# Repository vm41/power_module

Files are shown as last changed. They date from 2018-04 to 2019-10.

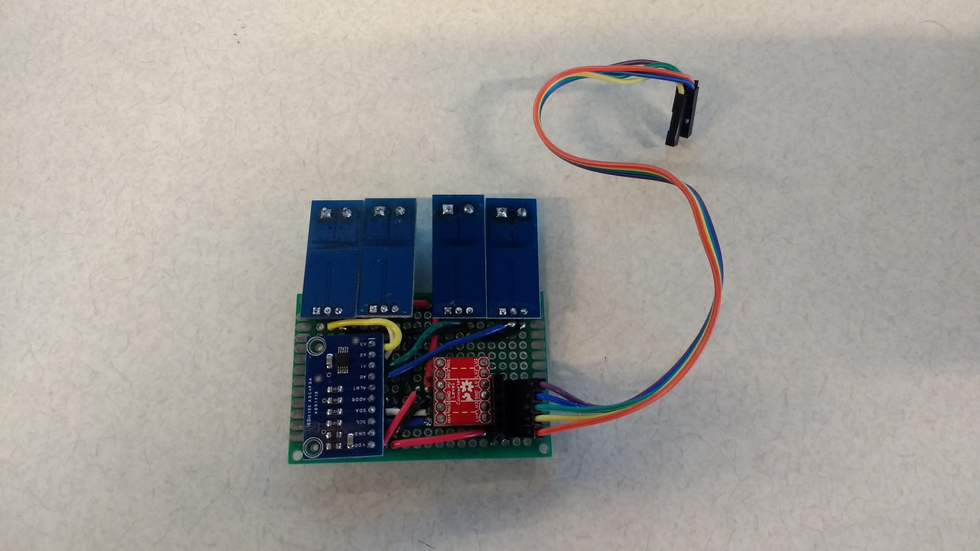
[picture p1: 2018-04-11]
hardware/photos/measurement-module-2.jpg

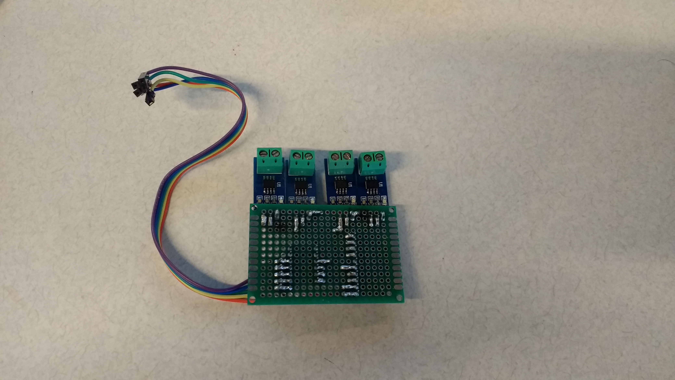
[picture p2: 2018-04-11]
hardware/photos/measurement-module-1.jpg

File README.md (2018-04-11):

# power_module
This repository is intended for use with current_sensing power module.

Documentations for selecting the hardware and instruments can be found in "doc"
Basic test scripts can be found in "i2c-test"

For running measurements:
- measure.py is the code to run on the drone, to measure motors currents, as well as receiving information from the agent, and recording them in log files.
- constant.py is a configuration file imported in measure.py
- tcp_client.py is a test code to run and act as the agent to send some commands to the measure.py manually.

All graph related scripts are in "graph", the ones in 2016 are not necessarily kept anymore, be careful.

---------------------------------------------------
measurement procedure:
* Note that the time of the system is correct before logging. if not, set it manually.
sudo date -s "2017-05-25 00:00"

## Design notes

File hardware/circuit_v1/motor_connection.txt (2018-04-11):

sensors
0	1	2	3
motors connected
B	A	D	C

Blue	Green	Red	Cyan

	^
Red  D	    A   Green

Cyan C      B   Blue

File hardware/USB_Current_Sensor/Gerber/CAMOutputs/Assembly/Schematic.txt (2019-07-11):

Partlist exported from /Users/jerinabr/Google Drive/Eagle_Projects/USB_Current_Sensor/Schematic.sch at 7/11/19 1:01 AM

Qty Value        Device       Package          Parts    Description                                                                            MPN          OC_FARNELL OC_NEWARK PACKAGE  SPICEPREFIX SUPPLIER         
2                2,54/1,0     2,54/1,0         GND, OUT THROUGH-HOLE PAD                                                                                                                                               
1   0.1uF        C-USC1808    C1808            C1       CAPACITOR, American symbol                                                                                                        C                            
1   0.5          R-US_R1206   R1206            R1       RESISTOR, American symbol                                                                                                         R                            
1   2k           R-US_R1206   R1206            R2       RESISTOR, American symbol                                                                                                         R                            
1   629004113921 629004113921 629004113921     K1       WR-COM Plug SMT With Clip USB Type A,4 pins=>Code : Con_I-O_COM_USB-2.0_A_629004113921                                                                         
1   62900416021  62900416021  62900416021      K2       WR-COM SMT Horizontal USB Type A,4 pins=>Code : Con_I-O_COM_USB-2.0_A_62900416021                                                                              
1   INA139NA/250 INA139NA/250 SOT95P280X145-5N U1       High-Side Measurement CURRENT SHUNT MONITOR                                            INA139NA/250 1470398    39C3949   SOT-23-5             Texas Instruments

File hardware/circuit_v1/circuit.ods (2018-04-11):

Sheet: design
 |  |  |  |  |  |  | ---
GND | OUT0 | VCC | GND | OUT1 | VCC |  |  |  | GND | OUT2 | VCC | GND | OUT3 | VCC
 | --- |  |  | --- |  |  |  |  |  | --- |  |  | ---
 |  |  |  |  |  |  |  | ---
 |  |  |  |  |  |  |  |  |  | --- | A3
 |  |  |  |  |  |  |  |  |  | --- | A2
 |  |  | LV1 |  |  | HV1 |  |  |  | --- | A1
 |  |  | LV2 |  |  | HV2 |  |  |  | --- | A0
 |  |  | LV |  |  | HV | --- |  |  |  | #
 |  |  | GND |  |  | GND |  | --- |  |  | ADD
 |  |  | LV3 |  |  | HV3 |  |  |  |  | SDA
 |  |  | LV4 |  |  | HV4 |  |  |  |  | SCL
 |  |  |  |  |  |  |  |  |  |  | GND
 |  |  |  |  |  |  |  |  |  |  | VCC

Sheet: TOP
 |  | --01-- |  |  |  | --01-- | --04-- | --02-- |  |  |  |  | --02-- | --03-- |  |  | --03--
GND | OUT0 | VCC |  | GND | OUT1 | VCC |  |  |  |  | GND | OUT2 | VCC |  | GND | OUT3 | VCC
--11-- | --- |  |  | --12-- | --- |  |  |  |  | --12-- | --13-- | --- |  |  | --13-- | ---
 |  |  |  | --11-- |  |  |  |  |  | --14--
 |  |  |  |  |  |  |  |  |  |  |  | --- | A3
 |  |  |  |  |  |  |  |  |  |  |  | --- | A2
 |  |  | LV1 |  |  |  | HV1 |  |  |  |  | --- | A1
 |  |  | LV2 |  |  |  | HV2 |  |  |  |  | --- | A0
 |  |  | LV |  |  |  | HV | --04-- | --05--
 |  |  | GND |  |  |  | GND | --16-- |  |  | --14-- | --15-- | ADD
 |  |  | LV3 |  |  |  | HV3 | --- |  |  |  | --- | SDA
 |  |  | LV4 |  |  |  | HV4 | --- |  |  |  | --- | SCL
 |  |  | --06-- |  |  |  |  |  |  |  | --16-- | --15-- | GND
 |  |  |  |  |  |  |  |  |  |  | --06-- | --05-- | VCC

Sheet: BACK
--03-- |  |  | --03-- | --02-- |  |  |  |  | --02-- | --04-- | --01-- |  |  |  | --01--
VCC | OUT3 | GND |  | VCC | OUT2 | GND |  |  |  |  | VCC | OUT1 | GND |  | VCC | OUT0 | GND
 | --- | --13-- |  |  | --- | --13-- | --12-- |  |  |  |  | --- | --12-- |  |  | --- | --11--
 |  |  |  |  |  |  | --14-- |  |  |  |  |  | --11--
 |  |  |  | A3 | ---
 |  |  |  | A2 | ---
 |  |  |  | A1 | --- |  |  |  |  | HV1 |  |  |  | LV1
 |  |  |  | A0 | --- |  |  |  |  | HV2 |  |  |  | LV2
 |  |  |  |  |  |  |  | --05-- | --04-- | HV |  |  |  | LV
 |  |  |  | ADD | --15-- | --14-- |  |  | --16-- | GND |  |  |  | GND
 |  |  |  | SDA | --- |  |  |  | --- | HV3 |  |  |  | LV3
 |  |  |  | SCL | --- |  |  |  | --- | HV4 |  |  |  | LV4
 |  |  |  | GND | --15-- | --16-- |  |  |  |  |  |  |  | --06--
 |  |  |  | VCC | --05-- | --06--

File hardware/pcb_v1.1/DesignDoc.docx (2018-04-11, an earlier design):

# overview

The objective of this project is to create a digital system capable of monitoring the power usage of multiple components involved in the operation of an autonomous unmanned aerial vehicle. The device will measure and record the power draw of each component to allow for accurate modeling of the system’s power consumption. In order to ensure accurate measurements without impeding the aircrafts operation the system should be lightweight and draw minimal power.

# design parameters

- Measure current draw of up to 20A
- High precision and accuracy measurements
- Record current draw of 8 separate devices
- Sample data points regularly at high speed
- Pass measurements to a higher level controller via I²C
- Support 3.3V and 5V logic systems
- Minimal weight/size
- Minimal power consumption

# block diagram

The first key components of the system are a set of eight current sensing devices. These sensors will be placed on the high side of each device to be measured and generate an analog output between ground and the logic voltage proportional to the current draw of the attached load. These analog values will then be sampled by an analog to digital converter (ADC) and the resulting digital values will be transmitted via an I²C serial interface to the high level controller.

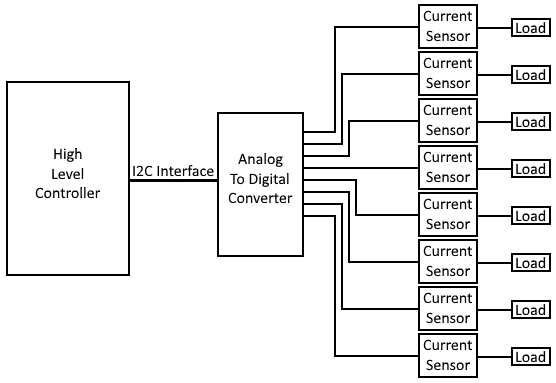
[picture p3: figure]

# Component selection

### A Note on Operating Voltage:

While the system as a whole needs to be able to operate on both 3.3V and 5V logic levels, this restriction is not necessarily needed for the operating voltage of all components in the system. As part of the I²C interface the master device pulls the clock and data lines high to its supply voltage. For some systems this is 3.3V while for others it is 5V. Conveniently this means that the logic voltage of the slave devices is not relevant (so long as it can handle the high voltage of the master) as it will only ever be pulling these lines down to ground, not up to its supply voltage. For example the Raspberry Pi is a 3.3V logic system, however this can be connected via I²C to an Arduino device operating with 5V logic. This is possible as logical high from the Raspberry Pi is 3.3V which falls above the 3V cutoff for the Arduino’s logical high.

As the entirety of this system is isolated from the master device by the I²C bus this allows us to choose components that operate on a standard 5V. This higher supply voltage allows the I²C interface to be operated with both 5V and 3.3V masters, provides greater dynamic range when generating analog voltages, and more greatly increases the list of available components to choose from. If 5V is not available in a given implementation an inline buck/boost converter can be added to regulate the supply voltage to 5V. A device like this devices is already integrated into the Raspberry Pi which provides a 5V output.

## Analog to Digital Converter:

The analog to digital converter used in this system will need to be able to receive 8 analog inputs and convert them to high precision digital values. This readings must be refreshed regularly to ensure that measurements reflect the changing current draw of each load. The device must also support an I²C interface to communicate with the high level controller.

### Resolution:

The accuracy of an ADC is largely determined by is resolution, the number of bits used to represent the digital values it generates. A higher resolution is desired as it directly increases a devices ability to sample an analog value accurately. For this implementation a resolution of 12 bits or more is likely desirable, this will guarantee accuracy within ~1.22 mV.

accuracy=(vcc)/(2^(resolution))=(5V)/(2^12)≈0.0012207 V

### Sampling Rate:

The sampling rate is the rate at which an ADC can convert analog values to digital ones. While this metric is not highly critical it is a factor to be considered. A higher sampling rate will allow conversion to be completed faster meaning that measurements will more accurately reflect the state of the system and will allow more data points to be collected. These values are measured in samples per second (S/s or sps) and can range from 10 S/s to 200kS/s depending on the device. A minimum of 1kS/s is recommended, for accuracy down to 1ms as loads may change quickly.

### Recommendation:

Based on these criteria I recommend we use the MAX11614EEE+ (https://www.mouser.com/ProductDetail/Maxim-Integrated/MAX11614EEE%2b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) analog to digital converter. It’s capable of reading 8 channels with 12 bit resolution at 94.4ksps and transmitting the results over I²C to a master operating at 3.3V or 5V. It also comes in a 12 channel version which could be implemented in the future if desired with minimal changes to the design.

## Current Sensor

### Functional Principle

The two most popular types of current sensors are Hall Effect current sensors and Current Shunt Monitors. Hall Effect sensors measure the electromagnetic field created by current flowing through a wire and produce an analog output proportional to the field strength. Shunt monitors pass the current over a small resistor and generate an analog output proportional to the voltage drop across the resistor, this allows the current flow to be calculated easily by Ohm’s law. These systems over differing tradeoffs between accuracy

### Accuracy and Range

The current sensors used in this system must be able to accurately measure currents ranging from 0-20A. Currents ≤ 1A are expected for computational components such as the higher level controller while peak currents of up to 20A may be drawn by the aircrafts motors. Due to this large range it may be difficult to accurately measure low current values.

One possible solution is for the device to have an adjustable gain, this would allow us to adjust the output ratio for each sensor individually and make full use of the sensors output range. For example let us consider a current sensor capable of measuring 0-20A and producing a corresponding output voltage of 0-5V. When connected to a motor drawing the full 20A maximum the sensor would produce an output voltage of 5V. However, when connected to a microcontroller drawing 1A or less the sensor would produce an output of 0.25V. In the second case the sensor is using at most 5% of its output range and in doing so loses accuracy to sample error and voltage fluctuations. Ideally we would adjust the gain of the sensor such that the maximum expected current, in this case 1A, generates the maximum possible output of 5V restoring the devices dynamic range.

While these voltage ranges and adjustable gain are possible with both Hall Effect sensors and shunt monitors, it is far easier to detect a wide range of voltages with a shunt monitor. When using a Hall Effect sensor to accurately measure current flows of <10A it is often necessary to add multi-layer or multi-wind paths as seen in the figure below to concentrate the magnetic field. Without these additions low current readings are likely to be unreliable. Unfortunately these traces are often incapable of handling currents >10A, meaning that we must choose at the time of the board design if a given channel will be able to measure 0A-10A accurately or 10A-20A accurately. This can be problematic if a load varies across these ranges, e.g. if a motor commonly draws 5A-15A.

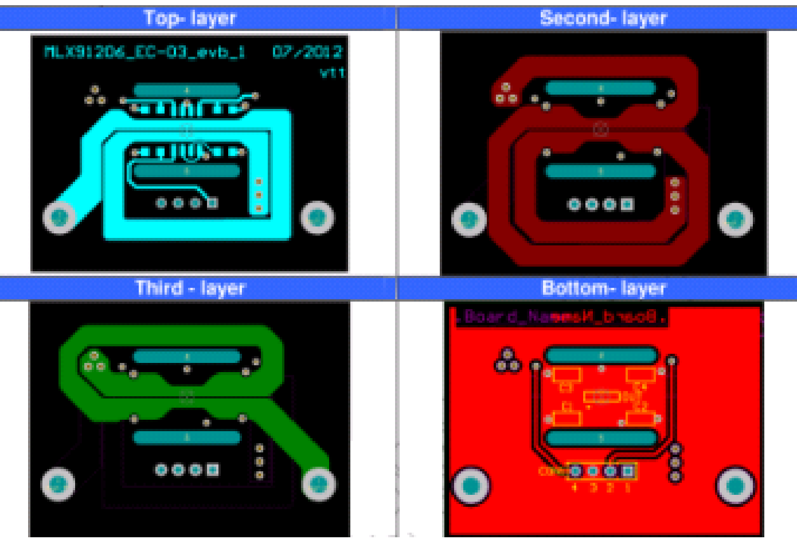
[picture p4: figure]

While Hall Effect sensors are moderately more accurate than shunt monitors given these modifications and proper tuning, shunt monitors are desirable for their ability smoothly measure current flow anywhere within the range set by their gain. The gain can be adjusted at any time simply by replacing a resistor on the output line allowing for precise measurements over a flexible range without requiring a redesign of the board itself.

### Isolation

When considering electrical isolation Hall Effect sensors are clearly superior. As Hall Effect sensors measure the magnetic field generate by the current and not the current directly they are non-intrusive and do not need to actually connect to a components power supply. This provides the benefit of an independent load and measurement system, a failure of one is unlikely to cause damage to the other as they are not physically connected. Contrastingly shunt monitors measure the current flow by passing it across a resistors and therefore need to be placed in line between the load and the voltage supply. Accordingly if a shunt resistor fails it may impede the operation of the load it is attached to, and excessively high load currents may damage the sensor itself. Under normal operation this shouldn’t matter but added isolation of a Hall Effect sensor is beneficial for fault protection.

### Complexity

While both Hall Effect Sensors and shunt monitors require passive components for proper operation, shunt monitors are a simpler a more robust option. A shunt monitor can be quickly and easily implemented with only the IC and two resistors. Hall Effect sensors are significantly more complex to setup accurately with recommended implementations using three capacitors, one resistor and a ferromagnetic shield. The shielding requirement is perhaps the most obtrusive, for accurate readings the manufacturer suggests using a U-shaped metal channel to focus the magnetic field from the load line and prevent interference from other electromagnetic sources. Given the application we can expect these sensors to be in close proximity to other components that will generate interference and make this shielding necessary. Lastly once constructed Hall Effect sensors should be tuned to ensure accurate readings. While these steps can ensure that Hall Effect sensors provide very accurate readings, they increase the chance of a manufacturing error or malfunction.

### Power Consumption

To be completed, want to run some calculations through MATLAB

### Recommendation

To be completed, dependent on results of MATLAB simulation

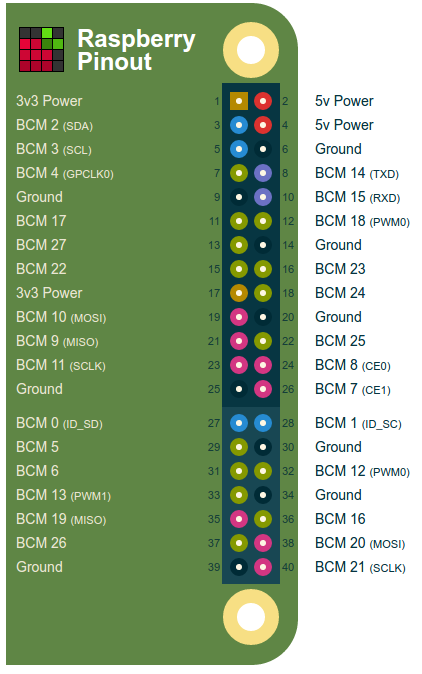
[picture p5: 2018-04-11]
hardware/photos/pi_pinout.png

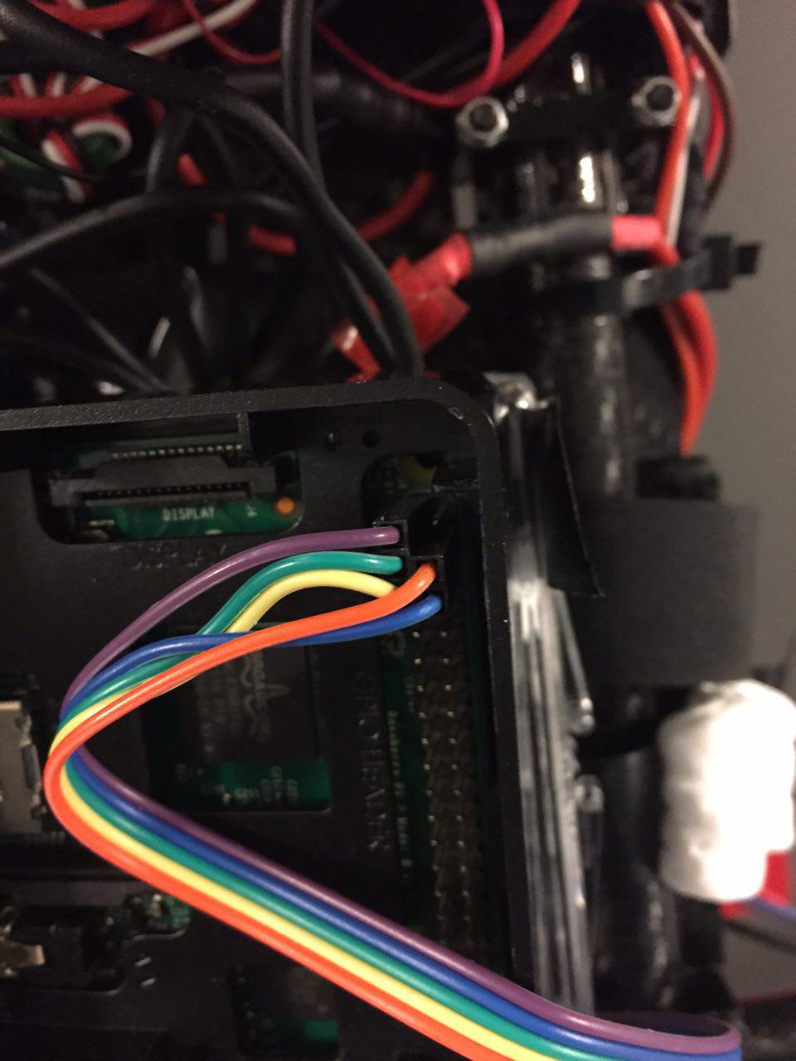
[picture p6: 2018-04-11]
hardware/photos/pi-connection.jpg

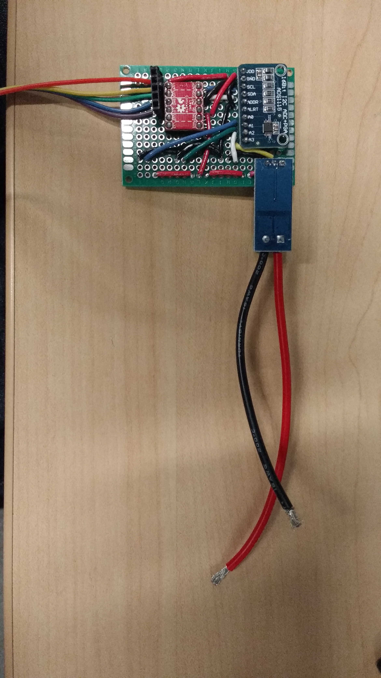
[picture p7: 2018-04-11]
hardware/photos/sensor-polarity-2.jpg

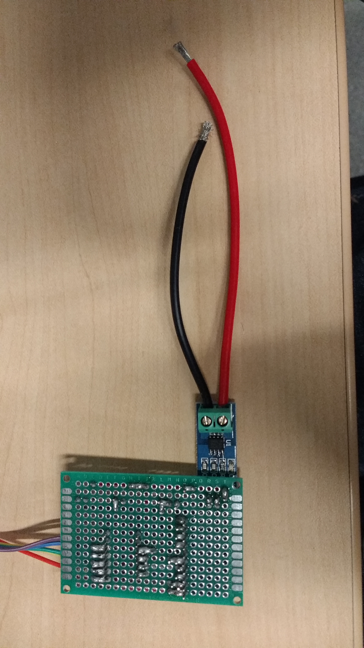
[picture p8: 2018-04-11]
hardware/photos/sensor-polarity-1.jpg

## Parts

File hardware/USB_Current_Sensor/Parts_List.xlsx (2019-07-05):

Number of Boards: | 3
Component | Quantity (per Board) | Quantity (Total) | Part Number | Price (per Part) | Price (Total) | Part Link
Current transducer | 1 | 3 | INA139NA/250 | $2.00 | $6.00 | digikey (https://www.digikey.com/product-detail/en/texas-instruments/INA139NA-250/INA139NA-250CT-ND/379721)
0.5ohm resistor | 1 | 3 | CSR1206FTR500 | $0.42 | $1.26 | digikey (https://www.digikey.com/product-detail/en/stackpole-electronics-inc/CSR1206FTR500/CSR1206FTR500CT-ND/3477074)
2kohm resistor | 1 | 3 | TNPW12062K00BEEA | $0.72 | $2.16 | digikey (https://www.digikey.com/product-detail/en/vishay-dale/TNPW12062K00BEEA/TNP2.00KACCT-ND/1857155)
0.1uF capacitor | 1 | 3 | VJ1808Y104KXCAT | $0.75 | $2.25 | digikey (https://www.digikey.com/product-detail/en/vishay-vitramon/VJ1808Y104KXCAT/720-1129-1-ND/1894475)
USB A Male | 1 | 3 | "629004113921" | $2.21 | $6.63 | digikey (https://www.digikey.com/product-detail/en/wurth-electronics-inc/629004113921/732-3182-5-ND/2627298)
USB A Female | 1 | 3 | "62900416021" | $2.36 | $7.08 | digikey (https://www.digikey.com/products/en?keywords=62900416021)
 |  |  |  | Price (per Board) | Price (Total boards)
 |  |  |  | $8.46 | $25.38

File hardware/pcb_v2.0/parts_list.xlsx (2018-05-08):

Number of Boards | 3 | Multiples of 3 only
Component | Quantity | Extd Quantity | Type/Value | Purpose | Package | Part Number | Price | Extended Price | Link
ADC | 1 | 3 | Analog to Digital Converter | take reads of IN0-IN7 |  | MAX11614EEE+ | $3.580 | $10.74 | mouser (https://www.mouser.com/ProductDetail/Maxim-Integrated/MAX11614EEE%2b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)
Voltage Regulator | 1 | 3 | linear regulator | make 3V3 for I2C bus | SOT-323-5L | LD59015C33R | $0.670 | $2.01 | mouser (https://www.mouser.com/ProductDetail/STMicroelectronics/LD59015C33R)
MOSFET | 2 | 6 | N Ch Enhancement | level shifters for I2C bus | SOT-23-3 | BSS138N H6327 | $0.290 | $0.87 | mouser (https://www.mouser.com/ProductDetail/Infineon-Technologies/BSS138N-H6327)
DC/DC Converter | 1 | 3 | 28V, 1.5A, 1.4MHz Step-Down Converter | buck converter for clean 5V from battery | SOT-23-6 | ACT4088US-T | $0.770 | $2.31 | mouser (https://www.mouser.com/ProductDetail/Active-Semi/ACT4088US-T)
 |  | 0 |  |  |  |  |  | $0.000
Passive Components |  | 0 |  |  |  |  |  | $0.000
Capacitor | 2 | 6 | .1uF ceramic | bypass for ADC vref/vcc | 0603 | VJ0603Y104JXQPW1BC | $0.100 | $0.30 | mouser (https://www.mouser.com/ProductDetail/Vishay-Vitramon/VJ0603Y104JXQPW1BC)
Capacitor | 2 | 6 | 1uF cermic | bypass for 3V3 regulator vcc/output | 0603 | VJ0603G105KXYCW1BC | $0.100 | $0.30 | mouser (https://www.mouser.com/ProductDetail/Vishay-Vitramon/VJ0603G105KXYCW1BC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)
Capacitor | 1 | 3 | undefined, possible .1uF above | voltage divider backup current | 0603 |  | $0.000 | $0.000
Capacitor | 2 | 6 | 22uF | stability of buck converter | 0603 | GRT188R60J226ME13D | $0.510 | 1.530 | mouser (https://www.mouser.com/ProductDetail/Murata-Electronics/GRT188R60J226ME13D?qs=5aG0NVq1C4wtE7eg0bKClQ%3d%3d)
Capactitor | 1 | 3 | 10uF | bypass for buck converter vcc | 0603 | C1608X5R0J106K080AE | $0.320 | 0.960 | mouser (https://www.mouser.com/ProductDetail/TDK/C1608X5R0J106K080AE)
 |  | 0 |  |  |  |  |  | $0.000
Resistor | 2 | 6 | 49.9k | feedback for buck, voltage divider | 0603 | APC0603B49K9N | $0.100 | $0.30 | mouser (https://www.mouser.com/ProductDetail/ARCOL-Ohmite/APC0603B49K9N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)
Resistor | 1 | 3 | 9.65k | feedback for buck, voltage divider | 0603 | RN731JTTD9651B25 | $0.630 | 1.890 | mouser (https://www.mouser.com/ProductDetail/KOA-Speer/RN731JTTD9651B25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)
Resistor | 4 | 12 | 10k | voltage divider pullups | 0603 | AC0603FR-0710KL | $0.016 | $0.05 | mouser (https://www.mouser.com/ProductDetail/Yageo/AC0603FR-0710KL)
 |  | 0 |  |  |  |  |  | $0.000
Inductor | 1 | 3 | 4.7uH | buck converter | 1008 | MLP2520V4R7MT0S1 | $0.420 | 1.260 | mouser (https://www.mouser.com/ProductDetail/TDK/MLP2520V4R7MT0S1)
Schottky Diode | 1 | 3 | 2A If, >28V Vrrm | buck converter | 0603 | NSR20F30NXT5G | $0.500 | 1.500 | mouser (https://www.mouser.com/ProductDetail/ON-Semiconductor/NSR20F30NXT5G)
 |  |  |  |  |  | Total Price Components |  | $24.02

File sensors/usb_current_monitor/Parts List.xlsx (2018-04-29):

No of Boards (mult of 3) | 3
Part | Part No | Quanity | Ext Quantity | Cost | Ext. Cost | Link
Shunt Monitor | INA169NA/3K | 1 | 3 | $2.21 | $6.63 | mouser (https://www.mouser.com/ProductDetail/Texas-Instruments/INA169NA-3K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)
Micro USB Connector | ZX62R-B-5P(30) | 1 | 3 | $0.93 | $2.79 | mouser (https://www.mouser.com/ProductDetail/Hirose-Connector/ZX62R-B-5P30)
USB Type A Connector | UJ2-AH-1-SMT-TR | 1 | 3 | $1.16 | $3.48 | mouser (https://www.mouser.com/ProductDetail/CUI/UJ2-AH-1-SMT-TR)
0.5Ω 0805 Shunt Resistor | LRCS0805-0R5FT5 | 1 | 3 | $0.17 | $0.51 | mouser (https://www.mouser.com/ProductDetail/IRC-TT-Electronics/LRCS0805-0R5FT5)
7.5kΩ 0805 Load Resistor | ERJ-PB6B7501V | 1 | 3 | $0.58 | $1.74 | mouser (https://www.mouser.com/ProductDetail/Panasonic/ERJ-PB6B7501V?qs=sGAEpiMZZMtlubZbdhIBIMNI7sOfyRuJfpLhIIhVJJY%3d)
Optional Headers - Ignore for now |  | 0 | 0 | $0.00 | $0.00
Signal Header Female | 505567-0371 | 0 | 0 | $0.73 | $0.00 | mouser (https://www.mouser.com/ProductDetail/Molex/505567-0371)
Signal Header Male | 505565-0301 | 0 | 0 | $0.25 | $0.00 | mouser (https://www.mouser.com/ProductDetail/Molex/505565-0301)
 |  |  | Total Cost: |  | 15.15

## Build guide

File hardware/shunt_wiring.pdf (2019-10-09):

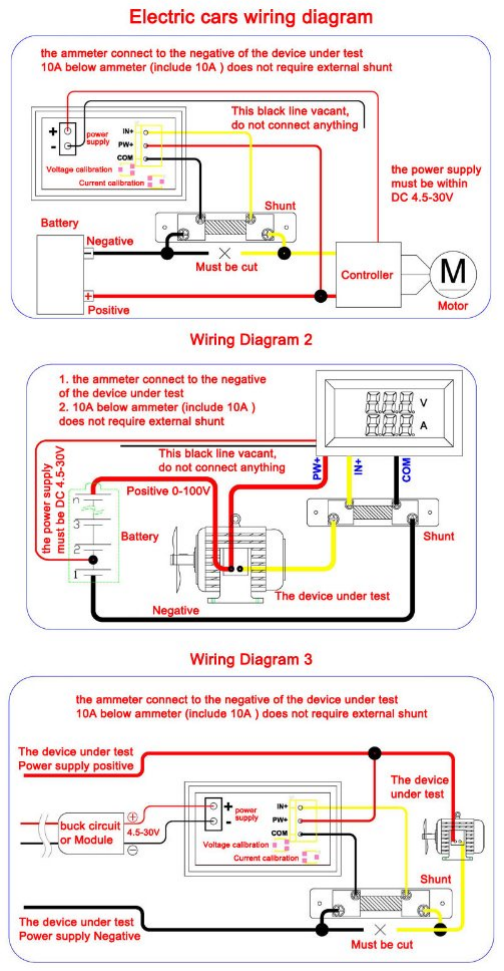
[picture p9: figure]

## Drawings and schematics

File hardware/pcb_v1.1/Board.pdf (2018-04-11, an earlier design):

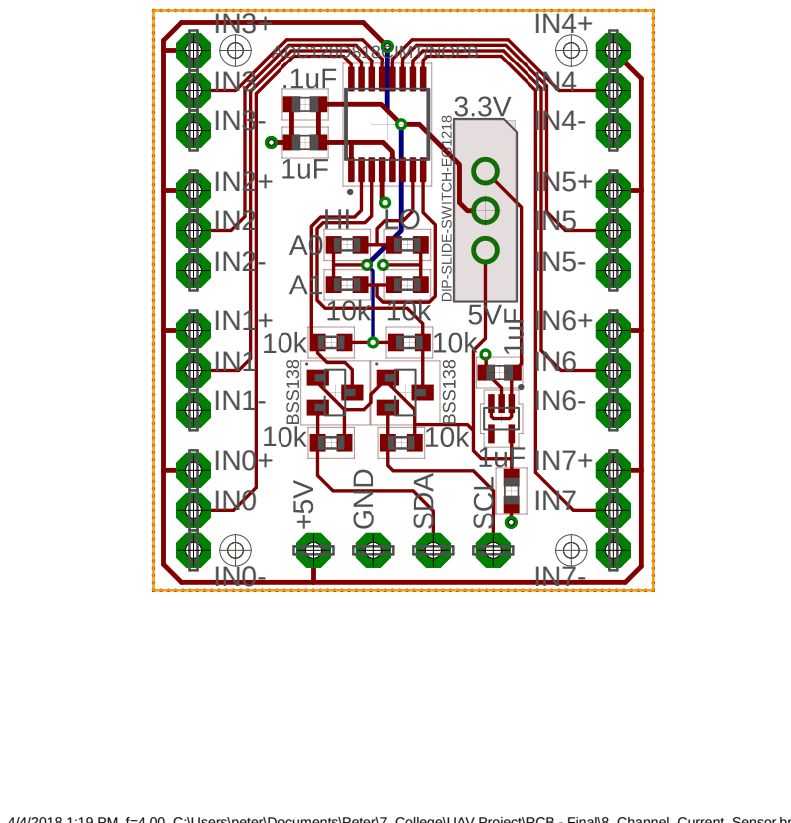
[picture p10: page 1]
GND; SDA; SCL; ADC128D818CIMT/NOPB .1uF

4/4/2018 1:19 PM f=4.00 C:\Users\peter\Documents\Peter\7. College\UAV Project\PCB - Final\8_Channel_Current_Sensor.brd

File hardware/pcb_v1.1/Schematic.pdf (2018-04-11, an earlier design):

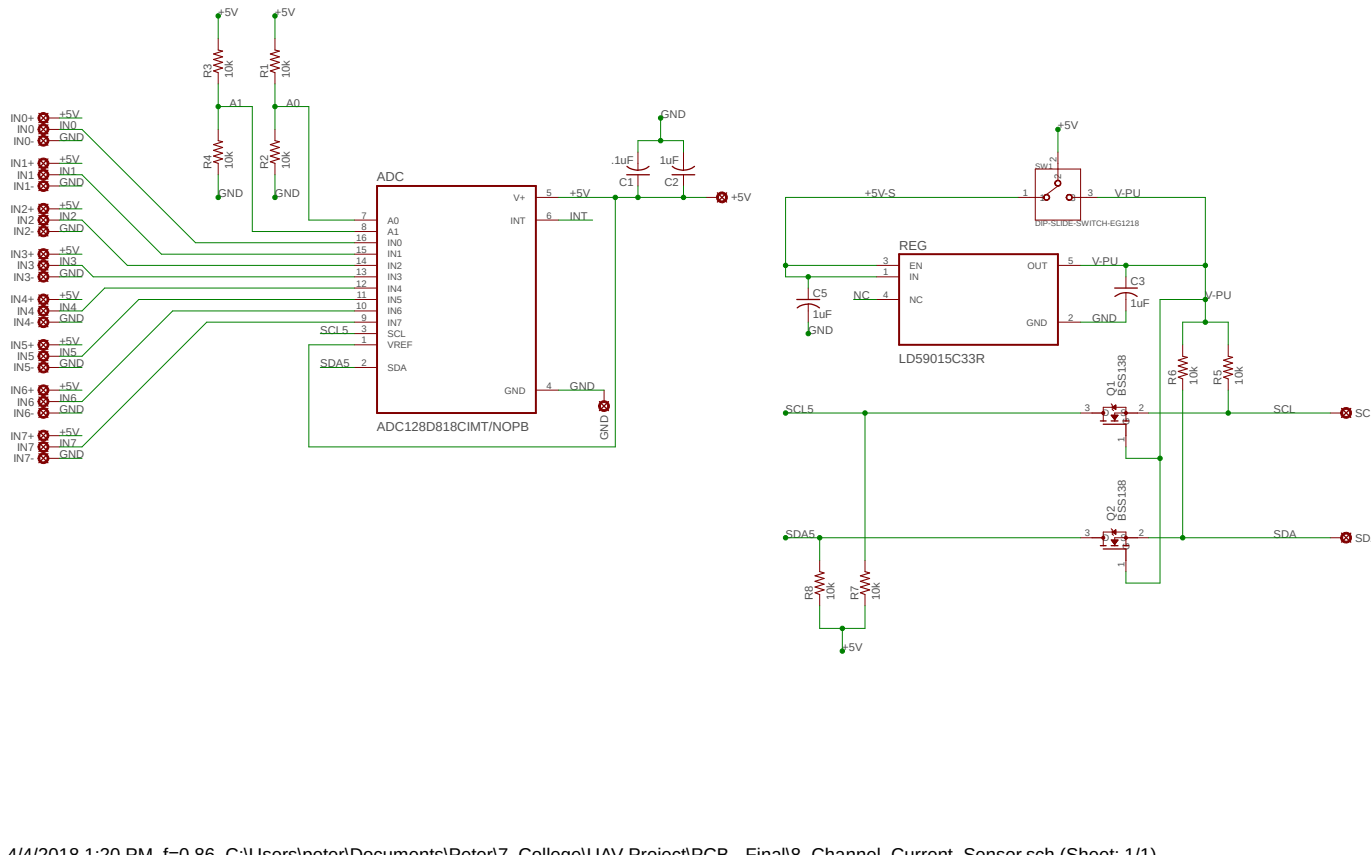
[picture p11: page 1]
ADC128D818CIMT/NOPB ¹⁰k 10k; DIP-SLIDE-SWITCH-EG1218 10k; BSS¹³⁸ BSS¹³⁸ 1uF ADC; SCL 3; VREF 1; SDA 2; INT; 6 GND; +5V GND; SCL SDA; REG; OUT; 5 GND; C3 GND; GND; GND GND GND GND GND GND GND GND GND; GND GND; INT SDA5; SDA5; SCL5

4/4/2018 1:20 PM f=0.86 C:\Users\peter\Documents\Peter\7. College\UAV Project\PCB - Final\8_Channel_Current_Sensor.sch (Sheet: 1/1)

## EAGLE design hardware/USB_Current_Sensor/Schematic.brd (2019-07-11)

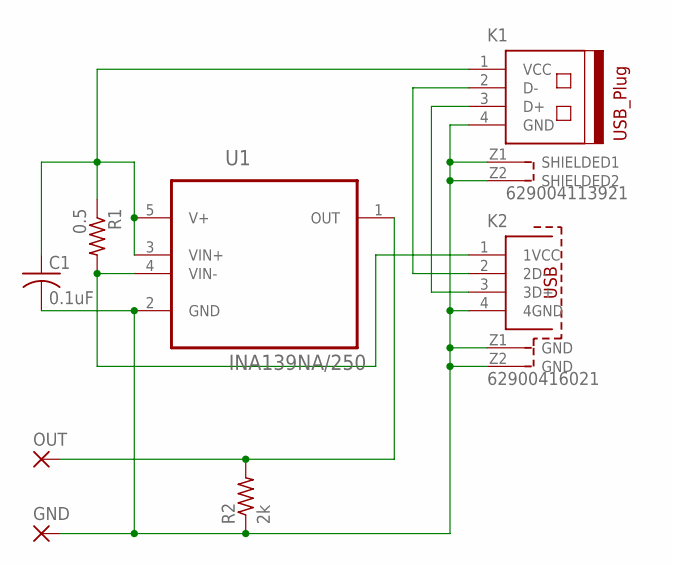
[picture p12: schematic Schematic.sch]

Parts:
C1: 0.1uF; C1808
GND: 2,54/1,0
K1: 629004113921
K2: 62900416021
OUT: 2,54/1,0
R1: 0.5; R1206
R2: 2k; R1206
U1: INA139NA/250; SOT95P280X145-5N

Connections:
unnamed: C1.2, GND.1, K1.4 (GND), K1.Z1 (SHIELDED1), K1.Z2 (SHIELDED2), K2.4 (4GND), K2.Z1 (GND), K2.Z2 (GND), R2.1, U1.2 (GND)
unnamed: K1.3 (D+), K2.3 (3D+)
unnamed: K1.2 (D-), K2.2 (2D-)
unnamed: C1.1, K1.1 (VCC), R1.1, U1.3 (VIN+), U1.5 (V+)
unnamed: OUT.1, R2.2, U1.1 (OUT)
unnamed: K2.1 (1VCC), R1.2, U1.4 (VIN-)

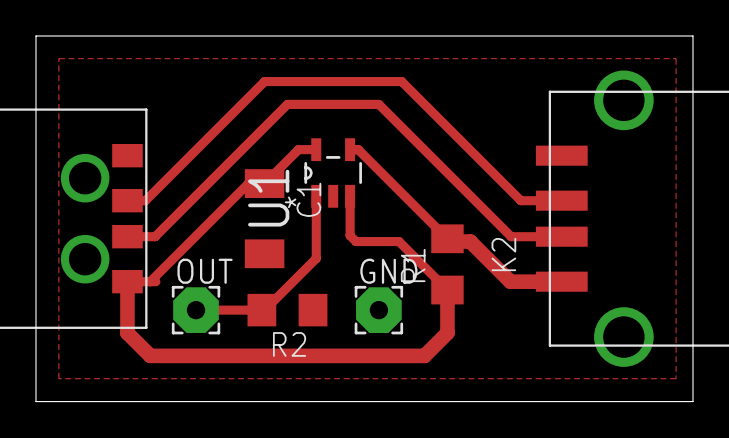
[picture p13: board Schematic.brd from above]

Board: 2 copper layers, 36.5 x 20.3 mm, 8 parts (0 on the bottom side), 6 nets.

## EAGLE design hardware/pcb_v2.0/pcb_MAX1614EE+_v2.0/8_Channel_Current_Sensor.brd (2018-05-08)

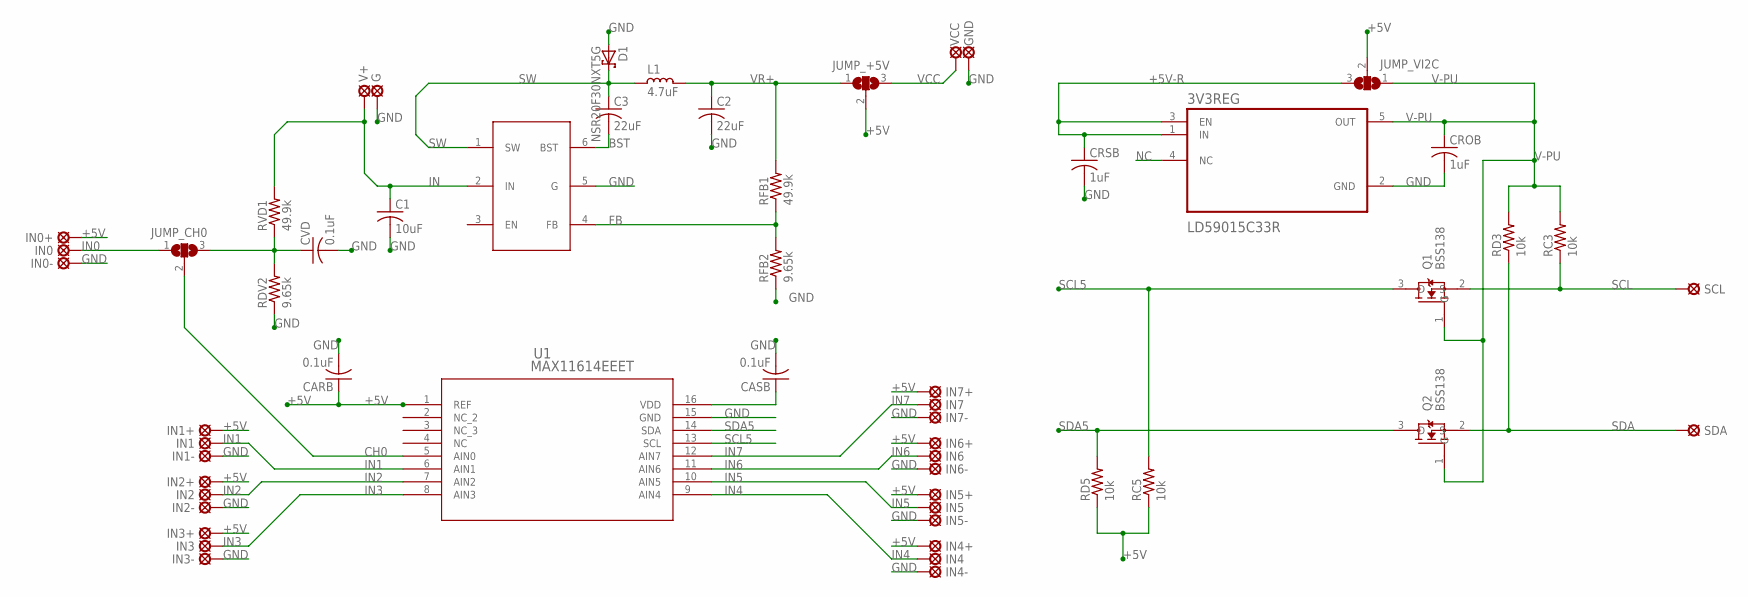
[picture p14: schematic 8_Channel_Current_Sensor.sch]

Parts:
3V3REG: LD59015C33R; SOT65P210X110-5N
5VBUCK: ACT4088US-T; SOT236
C1: 10uF; C0603K
C2, C3: 22uF; C0603K
CARB: 0.1uF; C0603
CASB: 0.1uF; C0603
CROB: 1uF; C0603
CRSB: 1uF; C0603
CVD: 0.1uF; C0603K
D1: NSR20F30NXT5G; C0603K
G: LSP10
GND: LSP10
IN0, IN0+, IN0-, IN1, IN1+, IN1-, IN2, IN2+, IN2-, IN3, IN3+, IN3-, IN4, IN4+, IN4-, IN5, IN5+, IN5-, IN6, IN6+, IN6-, IN7, IN7+, IN7-: LSP10
JUMP_+5V: SJ2W; SJ_2
JUMP_CH0: SJ2W; SJ_2
JUMP_VI2C: SJ2W; SJ_2
L1: 4.7uF; PM1008
Q1, Q2: BSS138; SOT95P240X120-3N
RC3, RC5: 10k; R0603
RD3, RD5: 10k; R0603
RDV2: 9.65k; R0603
RFB1: 49.9k; R0603
RFB2: 9.65k; R0603
RVD1: 49.9k; R0603
SCL: LSP10
SDA: LSP10
U1: MAX11614EEET; 21-0055H_16
V+: LSP10
VCC: LSP10

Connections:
+5V: CARB.1, CASB.1, IN0+.MP, IN1+.MP, IN2+.MP, IN3+.MP, IN4+.MP, IN5+.MP, IN6+.MP, IN7+.MP, JUMP_+5V.2, JUMP_VI2C.2, RC5.1, RD5.1, U1.1 (REF), U1.16 (VDD)
+5V-R: 3V3REG.1 (IN), 3V3REG.3 (EN), CRSB.1, JUMP_VI2C.3
BST: 5VBUCK.6 (BST), C3.2
CH0: JUMP_CH0.2, U1.5 (AIN0)
FB: 5VBUCK.4 (FB), RFB1.1, RFB2.2
GND: 3V3REG.2 (GND), 5VBUCK.5 (G), C1.2, C2.2, CARB.2, CASB.2, CROB.2, CRSB.2, CVD.2, D1.1 (A), G.MP, GND.MP, IN0-.MP, IN1-.MP, IN2-.MP, IN3-.MP, IN4-.MP, IN5-.MP, IN6-.MP, IN7-.MP, RDV2.1, RFB2.1, U1.15 (GND)
IN: 5VBUCK.2 (IN), C1.1, RVD1.2, V+.MP
IN0: IN0.MP, JUMP_CH0.1
IN1: IN1.MP, U1.6 (AIN1)
IN2: IN2.MP, U1.7 (AIN2)
IN3: IN3.MP, U1.8 (AIN3)
IN4: IN4.MP, U1.9 (AIN4)
IN5: IN5.MP, U1.10 (AIN5)
IN6: IN6.MP, U1.11 (AIN6)
IN7: IN7.MP, U1.12 (AIN7)
NC: 3V3REG.4 (NC)
SCL: Q1.2 (S), RC3.1, SCL.MP
SCL5: Q1.3 (D), RC5.2, U1.13 (SCL)
SDA: Q2.2 (S), RD3.1, SDA.MP
SDA5: Q2.3 (D), RD5.2, U1.14 (SDA)
SW: 5VBUCK.1 (SW), C3.1, D1.2 (C), L1.2
V-PU: 3V3REG.5 (OUT), CROB.1, JUMP_VI2C.1, Q1.1 (G), Q2.1 (G), RC3.2, RD3.2
VCC: JUMP_+5V.3, VCC.MP
VD: CVD.1, JUMP_CH0.3, RDV2.2, RVD1.1
VR+: C2.1, JUMP_+5V.1, L1.1, RFB1.2

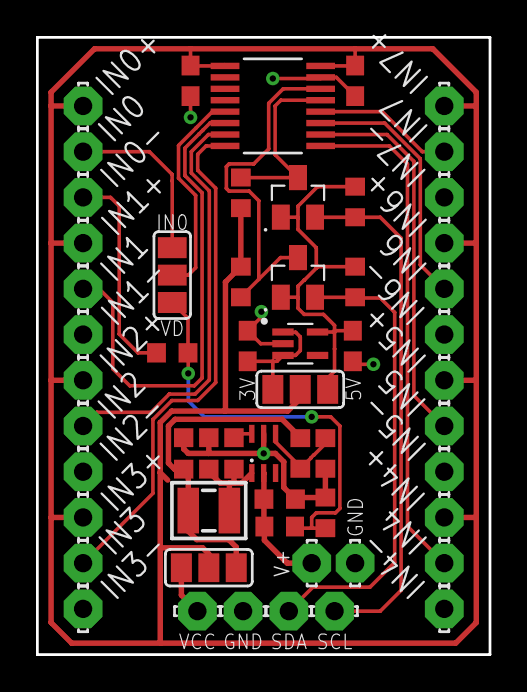
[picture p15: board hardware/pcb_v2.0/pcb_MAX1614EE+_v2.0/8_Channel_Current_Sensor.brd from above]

Board: 2 copper layers, 25.1 x 34.3 mm, 56 parts (0 on the bottom side), 24 nets.

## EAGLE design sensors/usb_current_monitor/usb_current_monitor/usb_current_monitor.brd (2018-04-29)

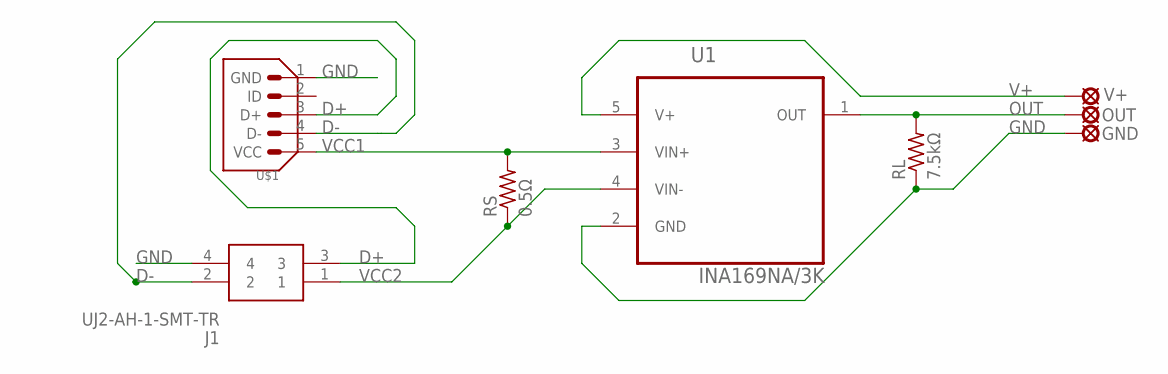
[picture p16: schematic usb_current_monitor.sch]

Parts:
GND: LSP10
J1: UJ2-AH-1-SMT-TR
OUT: LSP10
RL: 7.5kΩ; R0603
RS: 0.5Ω; R0603
U1: INA169NA/3K; SOT95P280X145-5N
U$1: ZX62R-B-5P
V+: LSP10

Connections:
D+: J1.3, U$1.3 (D+)
D-: J1.2, U$1.4 (D-)
GND: GND.MP, J1.4, RL.1, U1.2 (GND), U$1.1 (GND)
OUT: OUT.MP, RL.2, U1.1 (OUT)
V+: U1.5 (V+), V+.MP
VCC1: RS.2, U1.3 (VIN+), U$1.5 (VCC)
VCC2: J1.1, RS.1, U1.4 (VIN-)

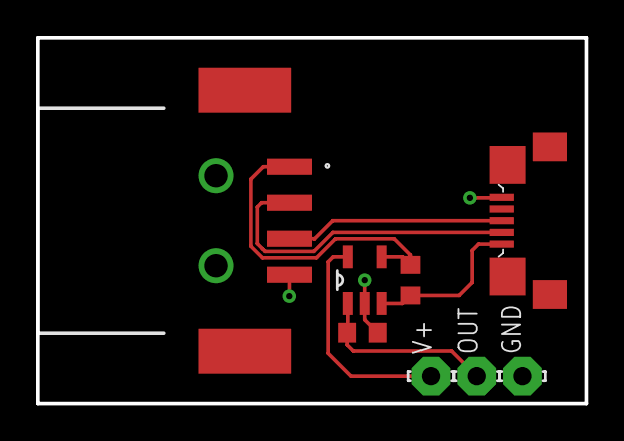
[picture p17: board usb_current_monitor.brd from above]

Board: 2 copper layers, 30.5 x 20.3 mm, 8 parts (0 on the bottom side), 7 nets.

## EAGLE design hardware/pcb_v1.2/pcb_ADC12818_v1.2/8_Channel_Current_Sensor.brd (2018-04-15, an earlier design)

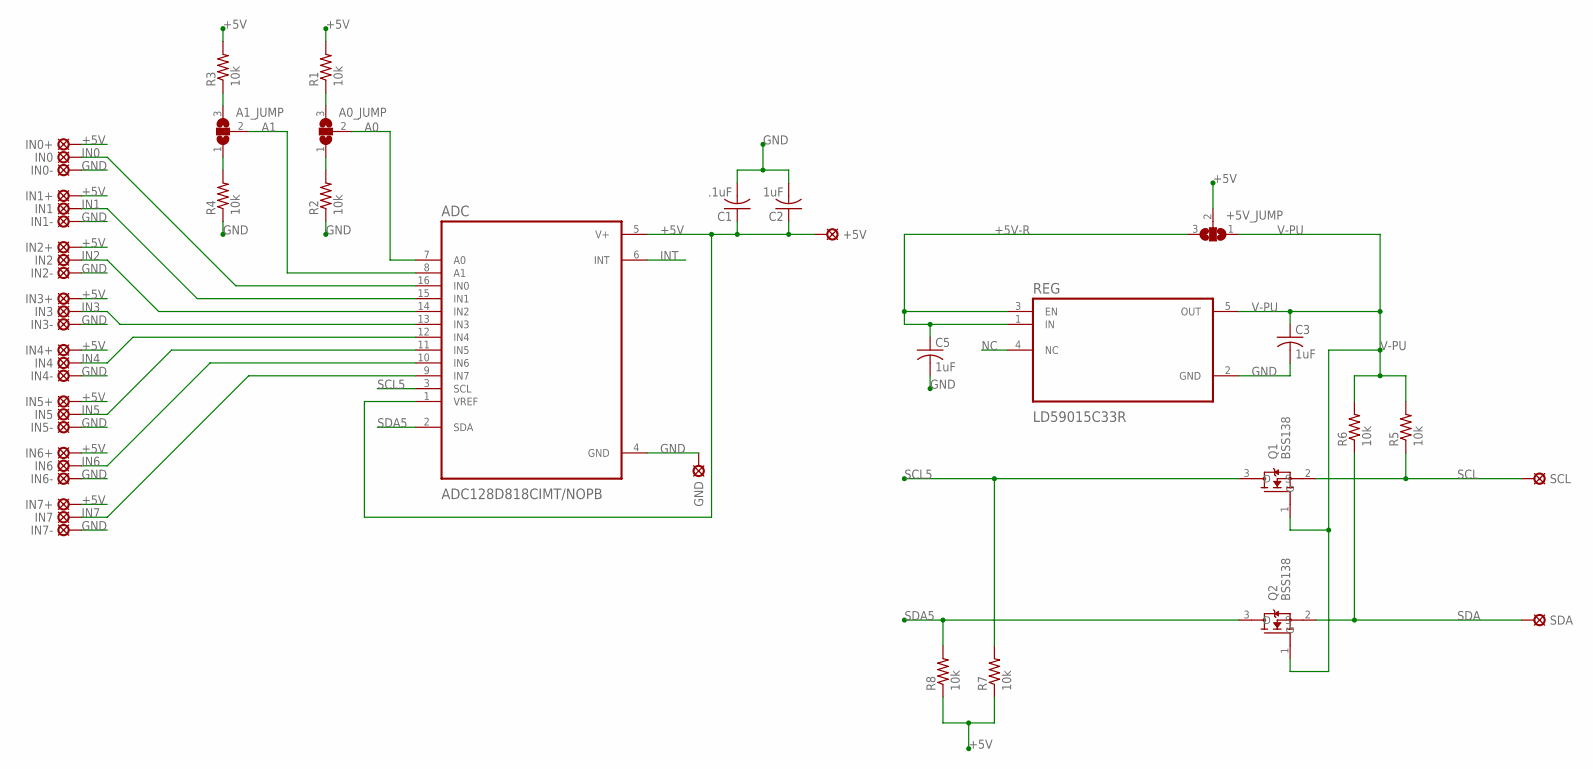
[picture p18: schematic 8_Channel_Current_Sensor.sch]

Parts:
+5V: LSP10
+5V_JUMP: SJ2W; SJ_2
A0_JUMP, A1_JUMP: SJ2W; SJ_2
ADC: ADC128D818CIMT/NOPB; SOP65P640X120-16N
C1: .1uF; C0603
C2, C3, C5: 1uF; C0603
GND: LSP10
IN0, IN0+, IN0-, IN1, IN1+, IN1-, IN2, IN2+, IN2-, IN3, IN3+, IN3-, IN4, IN4+, IN4-, IN5, IN5+, IN5-, IN6, IN6+, IN6-, IN7, IN7+, IN7-: LSP10
Q1, Q2: BSS138; SOT95P240X120-3N
R1, R2, R3, R4, R5, R6, R7, R8: 10k; R0603
REG: LD59015C33R; SOT65P210X110-5N
SCL: LSP10
SDA: LSP10

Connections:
+5V: +5V.MP, +5V_JUMP.2, ADC.1 (VREF), ADC.5 (V+), C1.1, C2.1, IN0+.MP, IN1+.MP, IN2+.MP, IN3+.MP, IN4+.MP, IN5+.MP, IN6+.MP, IN7+.MP, R1.2, R3.2, R7.1, R8.1
+5V-R: +5V_JUMP.3, C5.1, REG.1 (IN), REG.3 (EN)
A0: A0_JUMP.2, ADC.7 (A0)
A1: A1_JUMP.2, ADC.8 (A1)
GND: ADC.4 (GND), C1.2, C2.2, C3.2, C5.2, GND.MP, IN0-.MP, IN1-.MP, IN2-.MP, IN3-.MP, IN4-.MP, IN5-.MP, IN6-.MP, IN7-.MP, R2.1, R4.1, REG.2 (GND)
IN0: ADC.16 (IN0), IN0.MP
IN1: ADC.15 (IN1), IN1.MP
IN2: ADC.14 (IN2), IN2.MP
IN3: ADC.13 (IN3), IN3.MP
IN4: ADC.12 (IN4), IN4.MP
IN5: ADC.11 (IN5), IN5.MP
IN6: ADC.10 (IN6), IN6.MP
IN7: ADC.9 (IN7), IN7.MP
INT: ADC.6 (INT)
unnamed: A1_JUMP.3, R3.1
unnamed: A1_JUMP.1, R4.2
unnamed: A0_JUMP.1, R2.2
unnamed: A0_JUMP.3, R1.1
NC: REG.4 (NC)
SCL: Q1.2 (S), R5.1, SCL.MP
SCL5: ADC.3 (SCL), Q1.3 (D), R7.2
SDA: Q2.2 (S), R6.1, SDA.MP
SDA5: ADC.2 (SDA), Q2.3 (D), R8.2
V-PU: +5V_JUMP.1, C3.1, Q1.1 (G), Q2.1 (G), R5.2, R6.2, REG.5 (OUT)

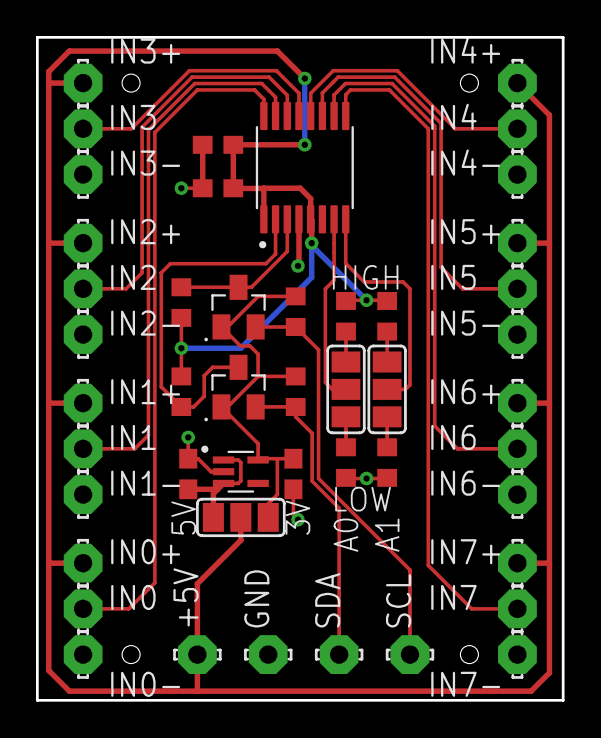
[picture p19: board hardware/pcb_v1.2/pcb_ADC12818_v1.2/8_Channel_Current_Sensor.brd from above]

Board: 2 copper layers, 29.2 x 36.8 mm, 47 parts (0 on the bottom side), 22 nets.

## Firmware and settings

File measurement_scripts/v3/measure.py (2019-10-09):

from constants import *
import sys
import os
import time
import random
import threading
from socket import *

# importing the ADC class file
from ADC128D818 import *
# importing the Transformation file
from Conversion import *
####### CUSTOMIZE ##########
DEVICE_ADDRESS = ADC_ADDRESS.LOW_LOW
##########################
#Mode selection
if MODE_SELECT == PROGRAM_MODE.PI:
    import smbus
    i2c = smbus.SMBus(1)
if MODE_SELECT == PROGRAM_MODE.PC:
    import Adafruit_GPIO.FT232H as FT232H
    FT232H.use_FT232H() # Temporarily disable FTDI serial drivers.
    ft232h = FT232H.FT232H() #Find the first FT232H device.
    i2c = FT232H.I2CDevice(ft232h, DEVICE_ADDRESS) # Create an I2C device at address.
if MODE_SELECT == PROGRAM_MODE.PC_SIMULATE_DATA:
    i2c = 0 #can't be undefined

dumpLock = threading.Lock()

class Measure(object):
    """Encapsulates all the necessary functions and attributes required for logging the current measurement:

    Attributes:
        LOG_MARK: description
        MARK_VALUE:
        LOG_EVENT:
        LOG_INFO:
        INFO_STRING:
        IS_LOGGING:
        FINISH_LOGGING:
        DUMP_FILE:
        SESSION_DIR:
        SESSION_DIR_INIT:
    Methods:
        open_session():
        dump(myStr):
    """



    def __init__(self, channels_to_measure):#one can pass i2c address here
        '''
        Initilisation goes here
        '''
        self.LOG_MARK                  = False
        self.MARK_VALUE                = 0
        self.LOG_EVENT                 = False
        self.LOG_INFO                  = False
        self.INFO_STRING               = ""
        self.IS_LOGGING                = False
        self.FINISH_LOGGING            = None
        self.DUMP_FILE                 = None
        self.SESSION_DIR               = None
        self.SESSION_DIR_INIT          = "session_"
        self.TCP_BUFF                  = 4096
        self.adc                       = adc
        self.CHANNEL_TO_MEASURE        = channels_to_measure
        if not os.path.exists(LOG_DIR):
            os.makedirs(LOG_DIR)
    # ###########################################################################################
    def open_session(self):
        session_id=1
        while os.path.exists(LOG_DIR+"/"+self.SESSION_DIR_INIT+"%03d"%(session_id)):
            session_id+=1
        self.SESSION_DIR=self.SESSION_DIR_INIT+"%03d"%(session_id)
        os.makedirs(LOG_DIR+"/"+self.SESSION_DIR)
        self.DUMP_FILE = open(LOG_DIR+"/"+self.SESSION_DIR+"/dump.log","a")
        #print self.SESSION_DIR

    # ###########################################################################################
    def dump(self, myStr):
        dumpLock.acquire()
        now = time.time()
        newStr = time.strftime("%Y_%m_%d_%H_%M_%S \t",
                time.localtime(now))+"%14.3f"%now+"\t"+myStr
        print newStr
        sys.stdout.flush()
        self.DUMP_FILE.write(newStr+"\n")
        self.DUMP_FILE.flush()
        dumpLock.release()
    ###########################################################################################
    def logging(self):
        time.sleep(0.1)
        self.dump("Start of logging thread")
        channel=0
        avg_count = 0
	reading_count = 0
        start_time=0
        finish_time=0
        start_time=time.time()
        last_time=start_time
        myFile_name = LOG_DIR+"/"+self.SESSION_DIR+"/log_"+time.strftime("%Y_%m_%d_%H_%M_%S", time.localtime(start_time))+"_power.log"# creating new file under current session directory
        self.dump("Opening file: %s"%(myFile_name))
        myFile=open(myFile_name,"a")
        myFile.write("#start time: %13.3f\t"%(start_time))
        myFile.write("\n")
        myFile.write(LOG_HEADER)
        myFile.write("\n")

        myBuffer=[]
        avg=[0.0]*self.adc.NUMBER_OF_CHANNELS
        while True:
            try:
                now=time.time()
                if ((reading_count / len(self.CHANNEL_TO_MEASURE)) % 100 == 0): #every 100 reading set, wait a bit to empty TCP buffer. sleep(0) has not worked very well?
                    time.sleep(0.001)
                if (channel==0):
                    time.sleep(0)
                    if (self.LOG_EVENT):
                        myLine="%14.3f\t%d"%(now,EVENT_TYPE.EVENT)
                        myBuffer.append(myLine)
                        self.LOG_EVENT=False
                        continue

                    if (self.LOG_MARK):
                        myLine="%14.3f\t%d\t%d"%(now,EVENT_TYPE.MARK,self.MARK_VALUE)
                        myBuffer.append(myLine)
                        self.LOG_MARK=False
                        continue

                    if (self.LOG_INFO):
                        myLine="%14.3f\t%d\t%s"%(now,EVENT_TYPE.INFO,self.INFO_STRING)
                        myBuffer.append(myLine)
                        self.LOG_INFO=False
                        continue

                    if (self.FINISH_LOGGING):
                        finish_time=now
                        myLine = "%14.3f: logged %d measurements. duration: %8.3f seconds. finishing up this log"%(now,avg_count,finish_time-last_time)
                        self.dump(myLine)
                        start_write=time.time()
                        myFile.write("\n".join(myBuffer))
                        myFile.flush()
                        self.dump("Flushing took " + str(time.time() - now) + " seconds")
                        break

                if (CHANNEL_SENSOR_MAP[channel][0] == SENSOR_TYPE.DISABLE):
                    channel=channel+1 #we need to skip the disabled channels.
                    if (channel>=self.adc.NUMBER_OF_CHANNELS):
                        channel=0
                    continue

                # new line, reading adc channel value
                raw_reading = self.adc.read_channel(channel)
                reading_count+=1 

                #convert the readings if required
                channel_data = Conversion.convert(CHANNEL_SENSOR_MAP[channel][0], raw_reading)

                ################
                myLine="%14.3f"%(now)+"\t"+str(EVENT_TYPE.MEASUREMENT)+"\t"+"%d"%(channel)+"\t"+"%6.2f"%(channel_data)
                myBuffer.append(myLine)                

                if (DEBUG_MODE):
                    avg[channel]+=channel_data
                    avg_count+=1
                    if (avg_count % (len(self.CHANNEL_TO_MEASURE)*VERBOS_AVERAGE_WINDOW) == 0):
                        myStr = "\n--- Average over last " + str(VERBOS_AVERAGE_WINDOW) + " measurements ---\n"
                        for i in range(0, self.adc.NUMBER_OF_CHANNELS):
                            if (i in self.CHANNEL_TO_MEASURE):
                                myStr += "channel " + str(i) + " " + str(avg[i] / VERBOS_AVERAGE_WINDOW) + "\n"
                        self.dump(myStr)
                        avg = [0.0] * self.adc.NUMBER_OF_CHANNELS
                        avg_count = 0

                if (reading_count >= LOG_BUFF_COUNT):
                    finish_time=now
                    start_write=time.time()
                    myLine = "%14.3f: logged %d measurements. duration: %8.3f seconds"%(now,reading_count,finish_time-last_time)
                    self.dump(myLine)
                    myFile.write("\n".join(myBuffer))
                    myFile.write("\n")
                    #myFile.flush()
                    self.dump("Emptying buffer took " + str(time.time() - start_write) + " seconds")
                    myBuffer=[]
                    last_time=finish_time
                    reading_count=0

		channel = channel+1
                if (channel >= self.adc.NUMBER_OF_CHANNELS):
                    channel = 0

            except Exception as e:
                self.dump("ERROR: some error in logging process, passing this loop: "+str(e))
                pass

        self.dump("End of logging thread here.")
        time.sleep(0)


if __name__ == '__main__':
    #create the ADC object
    # CUSTOMIZE
    adc = ADC128D818(i2c, DEVICE_ADDRESS)

    #intialize the ADC to 8 single ended inputs, external VREF, continuous  #sampling and no masked channels or interrupts
    #sampling and no masked channels or interrupts
    channels_to_measure = []
    for ch in range(adc.NUMBER_OF_CHANNELS):
        if (CHANNEL_SENSOR_MAP[ch][0] != SENSOR_TYPE.DISABLE):
            channels_to_measure.append(ch)

    #print "Channels to measure:", channels_to_measure

    # CUSTOMIZE
    adc.initialize(ADC_MODE.MODE_1, ADC_VREF.EXT, ADC_RATE.CONTINUOUS, channels_to_measure, 0)
    ##########################
    sensorLogger = Measure(channels_to_measure)#creating instance of the class object
    sensorLogger.open_session()
    sensorLogger.dump("--------------------------------------")
    sensorLogger.dump("STARTED PROGRAM")
    sensorLogger.dump("Writing logs to folder: %s"%(LOG_DIR+"/"+sensorLogger.SESSION_DIR))
    sensorLogger.dump("Make sure your constant.py file is set. MODE_SELECT, VDD, and LOG_DIR are important for logging")
    sensorLogger.dump("Currently these values are: %d, %5.3f, %s"%(MODE_SELECT, VDD, LOG_DIR))
    sensorLogger.dump("Channels to measure: "+str(channels_to_measure))

    #Here is where channels would be calibrated
    #call adc.calibrate(channel) for each channel that has an initial biased reading.
    #e.g the motors are initially off so their current
    #consumption is 0 while the PI will already be drawing current and therefore
    #can't be calibrated to account fo a zero input response
    for ch in channels_to_measure:
        if (CHANNEL_SENSOR_MAP[ch][1]): #calibrate flag
            adc.calibrate(ch)
            sensorLogger.dump("Channel %d initial reading at calibration: %f"%(ch, adc.read_bias(ch)))   
        else:
            adc.uncalibrate(ch)
            sensorLogger.dump("Channel %d initial reading: %f"%(ch, Conversion.convert(CHANNEL_SENSOR_MAP[ch][0], adc.read_channel(ch))))
            
    # CUSTOMIZE
    # uncalibrate any channel if needed
    #adc.uncalibrate(5) #this channel should be uncalibrated to read battery
    #sensorLogger.dump("Channel %d uncalibrated to 0.0"%(5))   
    adc.write_bias(5, VDD/2.0) # this channel is for pi energy, and needs to be manually calibrated
    sensorLogger.dump("Channel %d manually calibrated to %f"%(5,adc.read_bias(5)))

    ADDR = (PWR_HOST,PWR_PORT)
    serversock=socket(AF_INET,SOCK_STREAM)
    serversock.setsockopt(SOL_SOCKET, SO_REUSEADDR, 1)
    serversock.bind(ADDR)
    serversock.listen(5)

    sensorLogger.dump("Waiting for the client to connect to IP "+PWR_HOST)
    clientsock, add = serversock.accept()
    sensorLogger.dump("Client connected")
    corrupt_flag=False
    while True:
        try: 
            sensorLogger.dump("Waiting for a command from client")
            data=clientsock.recv(sensorLogger.TCP_BUFF)
            if data=="":
                #this would happen in case the client closes and wants to reopen.
                sensorLogger.dump("There seems to be something wrong with the socket, accepting another socket")

                # we are dependent on current session, so upon losing current
                # sesssion, we should finish our measurement and wait for next one to restart
                if TCP_CLIENT_DEPENDENT==True:
                    sensorLogger.dump("TCP_CLIENT_DEPENDENCY ist True, finishing up current session...")
                    if sensorLogger.IS_LOGGING==True:
                        sensorLogger.dump("Force finishing previous measurement")
                        sensorLogger.FINISH_LOGGING=True
                        myThread.join()
                        sensorLogger.IS_LOGGING=False
                        sensorLogger.dump("Child thread is done, this session is finished")
                    clientsock, add = serversock.accept()
                    sensorLogger.open_session()
                    sensorLogger.dump("--------------------------------------")
                    sensorLogger.dump("RESTARTING SESSION")
                    sensorLogger.dump("Writing logs to folder: %s"%(LOG_DIR+"/"+sensorLogger.SESSION_DIR))
                    sensorLogger.dump("Client connected")
                # if we are not dependent on current session, we will just
                # continue measuring, and wait for a possible connection without restart
                else:
                    sensorLogger.dump("TCP_CLIENT_DEPENDENCY ist False, ignoring the disconnection...")
                    clientsock, add = serversock.accept()
                    sensorLogger.dump("--------------------------------------")
                    sensorLogger.dump("Client connected")
                    sensorLogger.dump("CONTINUING PREVIOUS SESSOIN")
                continue
            sensorLogger.dump("Data received from client:" + repr(data))
            if (corrupt_flag==True):  #last buffer contained corrupt packet that we concatinate to this one
                sensorLogger.dump("WARNING: concatinating previous corrupt packet portion to this one")
                data=corrupt_packet + data
                corrupt_flag=False
            if not (data.endswith(PACKET_END)): # now we check if the new packet is in full form
                corrupt_packet=data.split(PACKET_END)[-1]
                corrupt_flag=True
                sensorLogger.dump("WARNING: packet seems to be corrupted and does not end with signature, considering it corrupt, and will concatinate it next time. corrupted portion: "+corrupt_packet)

            for command in data[0:data.rfind(PACKET_END)].split(PACKET_END): # only looking at full packets in data, so choosing the last occurance of PACKET_END as end of string
                if command=="":
                    continue
                #sensorLogger.dump("The number for command is: %d"%(int(command[0].encode("hex"),16)))
                if int(command[0].encode("hex"),16)==PWR_Command.PWR_START and sensorLogger.IS_LOGGING==False:
                    sensorLogger.LOG_EVENT = False
                    sensorLogger.LOG_MARK = False
                    sensorLogger.FINISH_LOGGING = False
                    sensorLogger.LOG_INFO = False
                    sensorLogger.INFO_STRING = ""
                    sensorLogger.IS_LOGGING=True
                    sensorLogger.dump("Logging thread starting from main thread")
                    myThread=threading.Thread(target=sensorLogger.logging)
                    myThread.start()
                    continue

                if int(command[0].encode("hex"),16)==PWR_Command.PWR_STOP and sensorLogger.IS_LOGGING==True:
                    sensorLogger.dump("Client wants to finish logging")
                    sensorLogger.FINISH_LOGGING=True
                    myThread.join()
                    sensorLogger.IS_LOGGING=False
                    sensorLogger.dump("Child thread is done, this session is finished")

                if int(command[0].encode("hex"),16)==PWR_Command.PWR_EVENT and sensorLogger.IS_LOGGING==True:
                    sensorLogger.dump("Client wants to record an event")
                    while(sensorLogger.LOG_EVENT):
                        pass
                    sensorLogger.LOG_EVENT=True

                if int(command[0].encode("hex"),16)==PWR_Command.PWR_MARK and sensorLogger.IS_LOGGING==True:
                    sensorLogger.dump("Client wants to make a numbered mark")
                    while(sensorLogger.LOG_MARK):
                        pass
                    sensorLogger.MARK_VALUE=int(command[1:].encode("hex"), 16)
                    sensorLogger.dump("Mark is: %d"%(sensorLogger.MARK_VALUE))
                    sensorLogger.LOG_MARK=True

                if int(command[0].encode("hex"),16)==PWR_Command.PWR_INFO and sensorLogger.IS_LOGGING==True:
                    sensorLogger.dump("Client has some info to log")
                    while(sensorLogger.LOG_INFO):
                        pass
                    sensorLogger.INFO_STRING=command[1:].decode('utf-8')
                    sensorLogger.dump("Info is: %s"%(sensorLogger.INFO_STRING))
                    sensorLogger.LOG_INFO=True

        except KeyboardInterrupt:
            sensorLogger.dump("\nInterrupted by user, waiting for logging to finish.")
            if sensorLogger.IS_LOGGING==True:
                sensorLogger.FINISH_LOGGING=True
                myThread.join()
                sensorLogger.dump("Child thread done")
            sensorLogger.dump("Now exiting program")
            time.sleep(1.0)
            exit()

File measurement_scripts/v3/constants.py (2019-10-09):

#import ADC128D818
#from ADC128D818 import *
class PWR_Command:
	PWR_START = 0
	PWR_STOP = 1
	PWR_EVENT = 2
	PWR_MARK = 3
	PWR_INFO = 4

class EVENT_TYPE:
	MEASUREMENT = 1
	EVENT = 2
	MARK = 3
	INFO = 4

class PROGRAM_MODE:
        PI = 0
    	PC = 1
    	PC_SIMULATE_DATA = 2

class SENSOR_TYPE:
    DISABLE = 0
    VOLTAGE = 1
    HALL = 2
    SHUNT = 3

class SENSOR_PURPOSE:
    NONE = 0
    BATTERY_VOLTAGE = 1
    MOTOR_CURRENT = 2
    DEVICE_CURRENT = 3

# CUSTOMIZE
MODE_SELECT = PROGRAM_MODE.PI#selected mode
VDD = 4.65 #actual voltage on a 5V pin powering the measurement module as float
DEBUG_MODE = False
VERBOS_AVERAGE_WINDOW = 1000

#if True (default), then the measurement will finish when tcp_client closes
#if false, the measurement will ocntinue after disconnection (and should probably be killed manually)
TCP_CLIENT_DEPENDENT=False

PWR_HOST = "127.0.0.1"
PWR_PORT = 35760
PACKET_END = '\r\r\n\n'
CALIBRATION_SAMPLES = 100


EARTH_R = 6371000.0 # radius of earth for calculations
REF_LONGITUDE = -78.79 # this may or may not be used within graph script
REF_LATITUDE = 43.009 # this may or may not be used within graph script



#LOG_BUFF_COUNT = number of readings before saving to file
if MODE_SELECT == PROGRAM_MODE.PI:
	LOG_BUFF_COUNT = 10000 
if MODE_SELECT == PROGRAM_MODE.PC:
	LOG_BUFF_COUNT = 1000
if MODE_SELECT == PROGRAM_MODE.PC_SIMULATE_DATA:
	LOG_BUFF_COUNT = 4000

LOG_DIR = "current"

#this string is just for information, it is printed
#on the second line of the log file after startTime
LOG_HEADER = "#time		#event_type	#event_data(channel&current(A), MarkNumber, ..."


# Defining type of sensor on each channel of the ADC.
# each cahnnel is a tuple, the first element is sensor type
# second element is a calibration flag (true is to calibrate and false is raw readings)
# third element is purpose type, is this sensor for a motor? is this measuring battery? or what?
# you may want to calibrate those channels only, that have a biased reading
# this list can be longer than needed (use for various number of channels)
# CUSTOMIZE
CHANNEL_SENSOR_MAP = [
        (SENSOR_TYPE.HALL, True, SENSOR_PURPOSE.MOTOR_CURRENT),           #channel 0
        (SENSOR_TYPE.HALL, True, SENSOR_PURPOSE.MOTOR_CURRENT), 
        (SENSOR_TYPE.HALL, True, SENSOR_PURPOSE.MOTOR_CURRENT),
        (SENSOR_TYPE.HALL, True, SENSOR_PURPOSE.MOTOR_CURRENT), 
        (SENSOR_TYPE.VOLTAGE, False, SENSOR_PURPOSE.BATTERY_VOLTAGE),
        (SENSOR_TYPE.HALL, False, SENSOR_PURPOSE.DEVICE_CURRENT),
        (SENSOR_TYPE.SHUNT, False, SENSOR_PURPOSE.DEVICE_CURRENT), 
        (SENSOR_TYPE.DISABLE, False, SENSOR_PURPOSE.NONE),
        (SENSOR_TYPE.DISABLE, False, SENSOR_PURPOSE.NONE),
        (SENSOR_TYPE.DISABLE, False, SENSOR_PURPOSE.NONE),
        ]

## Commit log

2018-04-11 Migrating to new repo, squash all commits up to Fall 2017.
    [circuit.ods, sensor_config.txt]
2018-04-11 added gitignore file, currently ignoring the current folder, contains dummy data
2018-04-11 fixed one bug related to failure in calibration
    [constants.py, measure.py, measure2.py]
2018-04-11 pre liminary schematic for current sensor
    [pcb.kicad_pcb, pcb.sch]
2018-04-11 mew schematic uploaded
    [8channel.kicad_pcb, 8channel.sch, pcb.kicad_pcb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]
2018-04-11 Added Eagle schematics, libraries and design material for ADC board
2018-04-11 Added hardware datasheets and unzipped redesign file
    Unzipped redesign folder and added datasheets for ADC and voltage regulator for reference
    [8_Channel_Current_Sensor.brd, 8_Channel_Current_Sensor.sch, Parts List.xlsx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]
2018-04-11 organazied completely, logs taken out, this is now only power_module regardless of the project
    [8_Channel_Current_Sensor.brd, 8_Channel_Current_Sensor.sch, 8channel.kicad_pcb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]
2018-04-11 added new sensor datasheet and partial config
    [ADC128d818_config.txt, ADS1115_config.txt]
2018-04-13 Implemented object oriented approach to ADC reading
    Created a python file called "ADC128D818.py" which contains a class and all neccessary constants to create, initialize, and read from the ADC as its own object. The measure.py code was updated to uti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
2018-04-15 New PCB designs, reorganized files, removed clutter
    Added pcb v1.2 the final draft of the ADC12818 board.
    Added pcb v2.0 the new board boased on the MAX1614EE+ ADC
    Added datasheet for MAX ADC
    Renamed folders to have consistent naming scheme
    Removed unncessary tempoary files
    [8_Channel_Current_Sensor.brd, 8_Channel_Current_Sensor.sch, 8channel.kicad_pcb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]
2018-04-16 fixed a couple of bugs related to PI reading
    [ADC128D818.py, constants.py, i2c_utilities.py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]
2018-04-19 seached for bug, was able to take successful live readings, tested channel disabling, disabled all unused channels
    [measure.py, measure2.py]
2018-04-25 Bug fixes
    Removed adc.stop() from measure.py and moved it into the initializtion function of the adc class
    [ADC128D818.py, constants.py, measure.py]
2018-04-25 Bug fixes
    small changed to unsused class
    [measure2.py]
2018-04-26 restructured a bit, added feature to select channels to measure, added voltage divider channel to measure battery, has not yet been tested on hardware
2018-04-29 added pcb designs for usb current monitor
    Added datasheets, libraries, part list, and design for a custom cirucut board which provides passthrough USB power and monitors the current being drawn by the attached device
    [Parts List.xlsx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]
2018-04-29 error correction on usb current monitor board
    Flipped VIN+ and VIN- on the current sensor to conform with correct direction of current flow
    [bottom_copper.gbl, bottom_silkscreen.gbo, bottom_soldermask.gbs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]
2018-05-08 Finished v2 of ADC board
    Completed changes to ADC board and parts list.
    Changes:
    -Added header for voltage directly from the battery
    -Added voltage divider to measure battery voltage
    -Added buck converter to make clean 5V from battery voltage
    -Switched to more accurate MAX1614 ADC
    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
    [8_Channel_Current_Sensor.brd, 8_Channel_Current_Sensor.sch, parts_list.xlsx]
2018-05-22 code restructured to prevent logging for disabled channels
    [ADC128D818.py, constants.py, measure.py]
2018-06-07 Added Gerber Files for ADC board v2
    Generated Gerber files using the Oshpark CAM file I created. Gerber files can now be sent for manufacture of boards and stencils
    [bottom_copper.gbl, bottom_silkscreen.gbo, bottom_soldermask.gbs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]
2018-06-08 fixed random in PC_SIMULATE_DATA mode
    [i2c_utilities.py, measure.py]
2018-06-12 fixed syntax. flushing take ~30 ms, maybe it should not be explicitly asked for.
    [measure.py]
2018-06-12 The output flushing was getting clogged, changed it to one write command only, and removed flush syntax. Furthermore, two threads had a clogging issue, losing TCP request timings, fixed it by force y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
    [constants.py, measure.py]
2018-06-19 added graph files for current sensor and voltage sensor
2018-06-20 fixed a bug in logger module, added a preprocessing script, modified graph script for UB-ANC experiments
    [measure.py]
2018-06-21 updated git ignore to exclude current folder in graphs
2018-06-26 dumping calibration values, added read_bias to the ADC, removing extra prints
2018-07-10 updated measure so it stops measurement thread upon TCP disconnection
2018-07-19 MAJOR COMMIT. introduced channel-motor mapping, adde hover setup, and combined all into TARGET_SETUP, added flag for STEADY DETECTION, added PATH graphing and animation, introduced LAN/LON reference,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
2018-07-19 added SENSOR_PURPOSE mapping
2018-09-10 added a wait every 100 reading set, in order to empty TCP buffer. sleep(0) may have not worked properly. Also introduced corrupt packet detection and concatination with next packet. ignoring half pac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
    [measure.py]
2018-10-10 fixed a typo for uncalibrating the battery voltage channel 4
    [measure.py]
2018-10-10 tcp_client was case sensitive, now it accepts lower case comands too
2018-10-10 added TCP_CLIENT_DEPENDENCY option, for better handling session disconnections. Updated TCP client interface, also fixing support for markers
    [constants.py, measure.py, tcp_client.py]
2019-07-06 Zipped Gerber files for PCB manufacturing
2019-07-06 Gerber Files
    [copper_top.gbr, drill_1_16.xln, gerber_job.gbrjob]
2019-07-11 PCB design for usb current monitor
    [Schematic.brd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]
2019-08-16 Modified the power_module to be used with erle-copter -Changed ADC address from "LOW_LOW" to "MID_MID" -Changed the channel sensor map to reflect the channels used on the ADC -Added the shunt convers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
2019-10-06 moving back to UB-ANC platform, adding extr channels for DEVICE measurements, introducing START_TIME and DURATION for graphing.
2019-10-09 reverted conversion of HALL sensor to simple scale. (remember to handle calibration/uncalibration in measrement). working on plot script, ongoing...
    [constants.py, measure.py]
2019-10-09 Jerin fixed errors, and updated calibration for kinect experiment
    [constants.py, measure2.py, tcp_client2.py]
2019-10-09 manual calibration added for device hall sensors (not tested yet)
2019-10-09 Added second hall sensor for barrel connector, fixed case where USB sensor reading would go above max voltage
    [measure2.py]

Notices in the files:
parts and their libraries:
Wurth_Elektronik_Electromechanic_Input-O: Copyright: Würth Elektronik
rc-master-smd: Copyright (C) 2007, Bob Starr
